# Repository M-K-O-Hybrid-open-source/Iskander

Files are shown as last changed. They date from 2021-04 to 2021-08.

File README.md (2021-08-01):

# Iskander
Iskander is an open source driver for low voltage **DC**, **BLDC**, **PMSM** motors, amde specifically for education and learning.
the repo containts some example ocodes and SIMULINK modeles to help you get started.
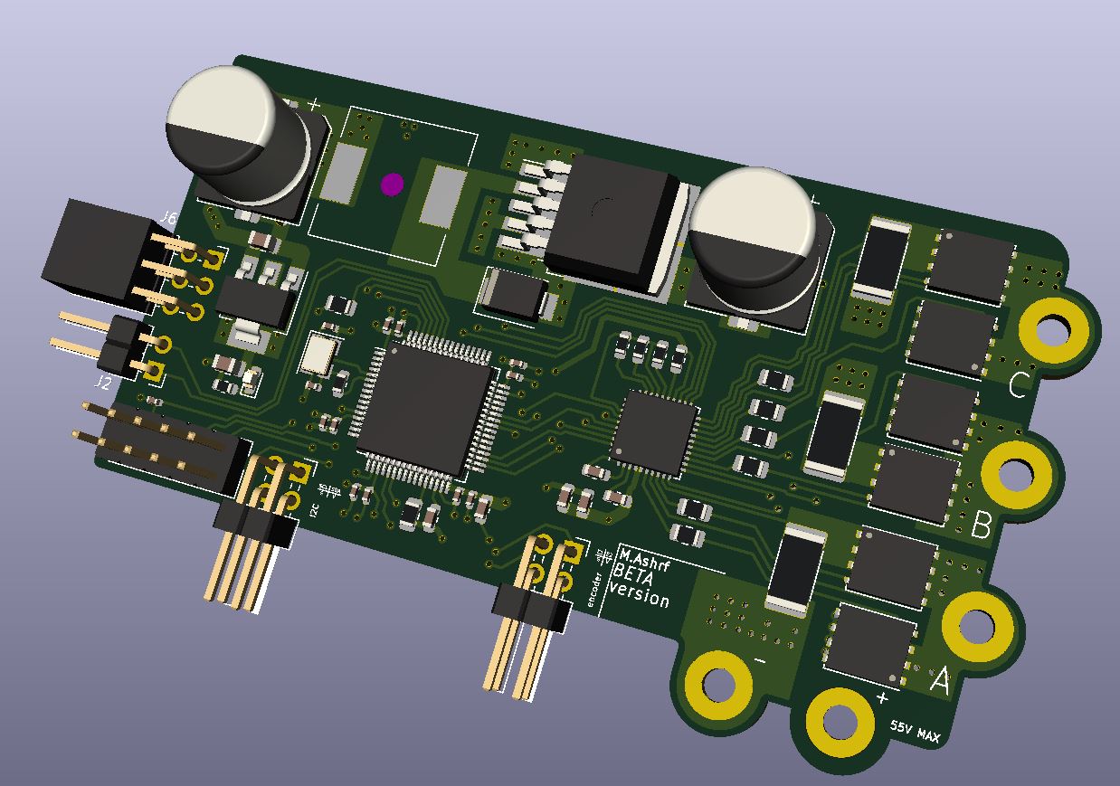
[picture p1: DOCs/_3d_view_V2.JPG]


# Main HARDWARE
- STM32f446RE (main micro-controller)
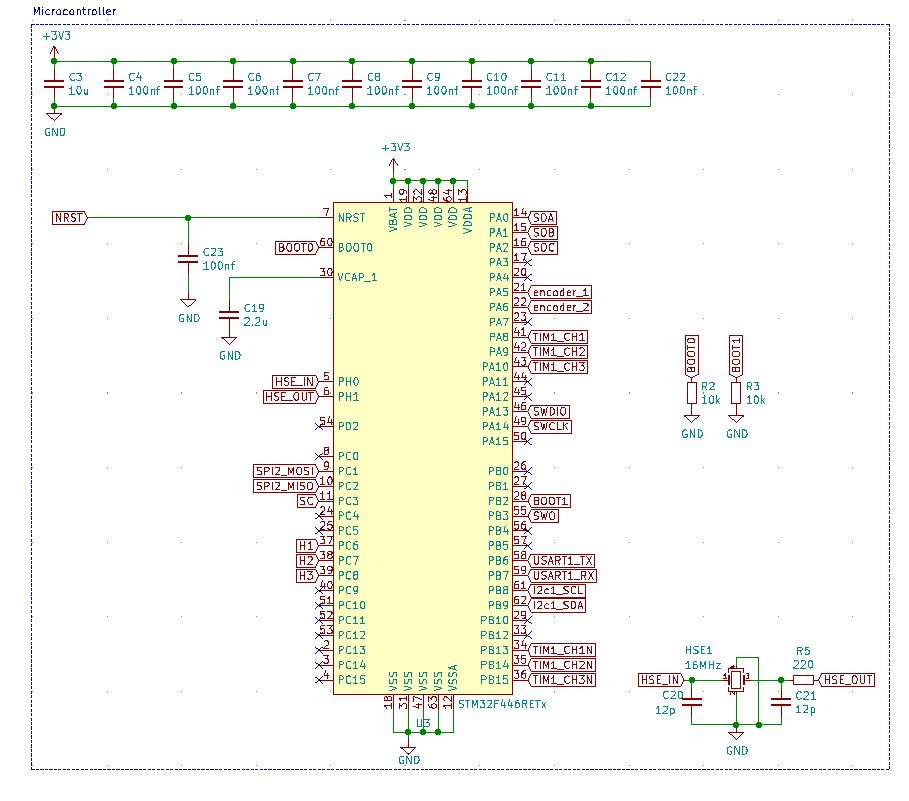
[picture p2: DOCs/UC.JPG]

- DRV8323H (mosfet driver and current sensors)
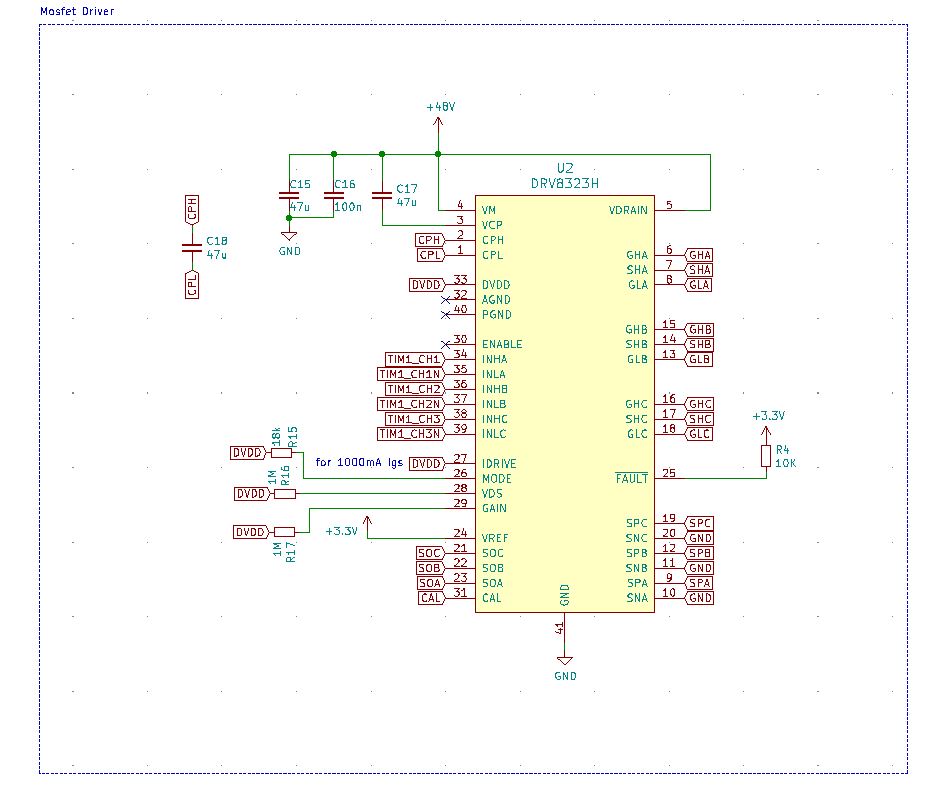
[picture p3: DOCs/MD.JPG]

- CSD19534Q5A (MOSFETs)
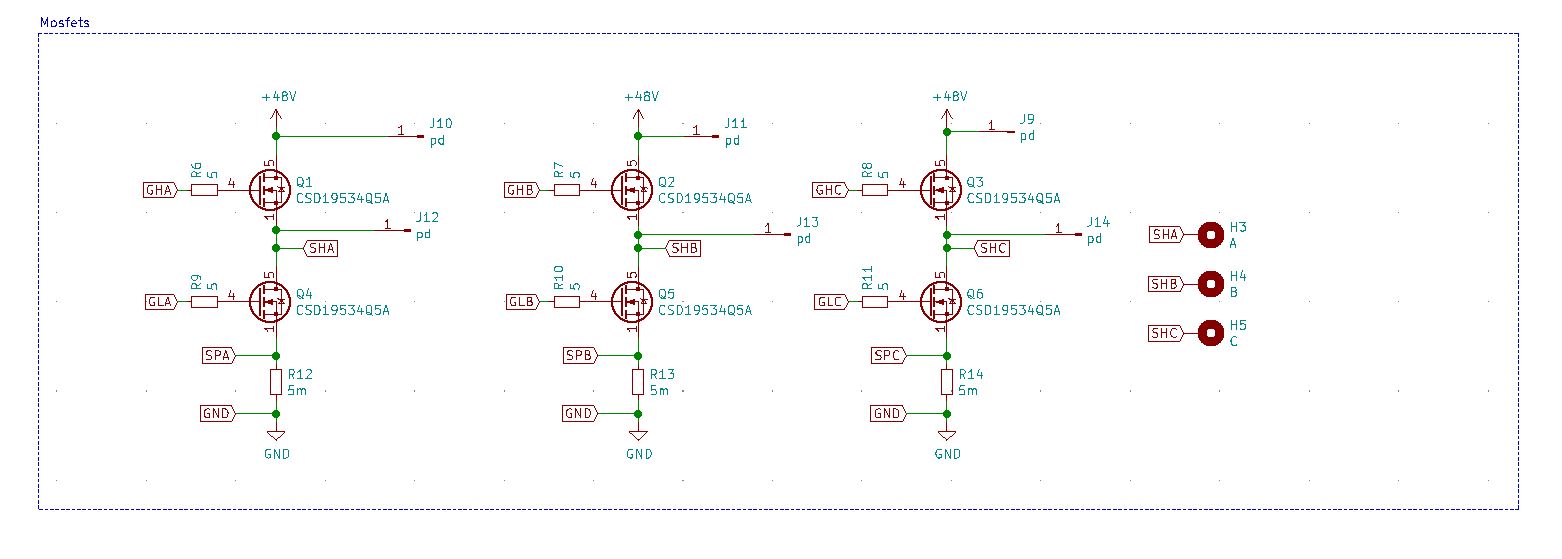
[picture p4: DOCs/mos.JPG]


# the hardware supports the following drives
### DC motor supported drives
- open/closed loop speed control.
- torque control.
- cascadded control.
- position control.

### BLDC motor supported drives
- open/closed loop sensored speed control (Hall effect sensors)
- sensored cascadded control.

### PMSM motor supported drives
- sensored FOC control.
- sensorless control using MRAS as speed estimator(currently under testig).
- sensorless control using EKF as speed estimator(currently under testig).

# PCB layout
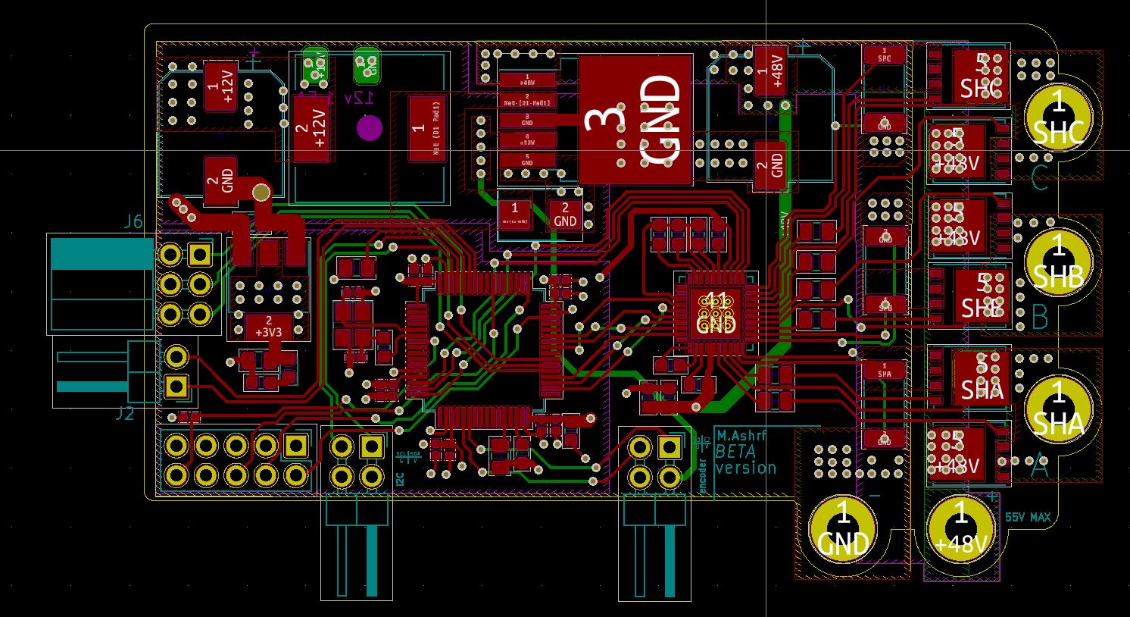
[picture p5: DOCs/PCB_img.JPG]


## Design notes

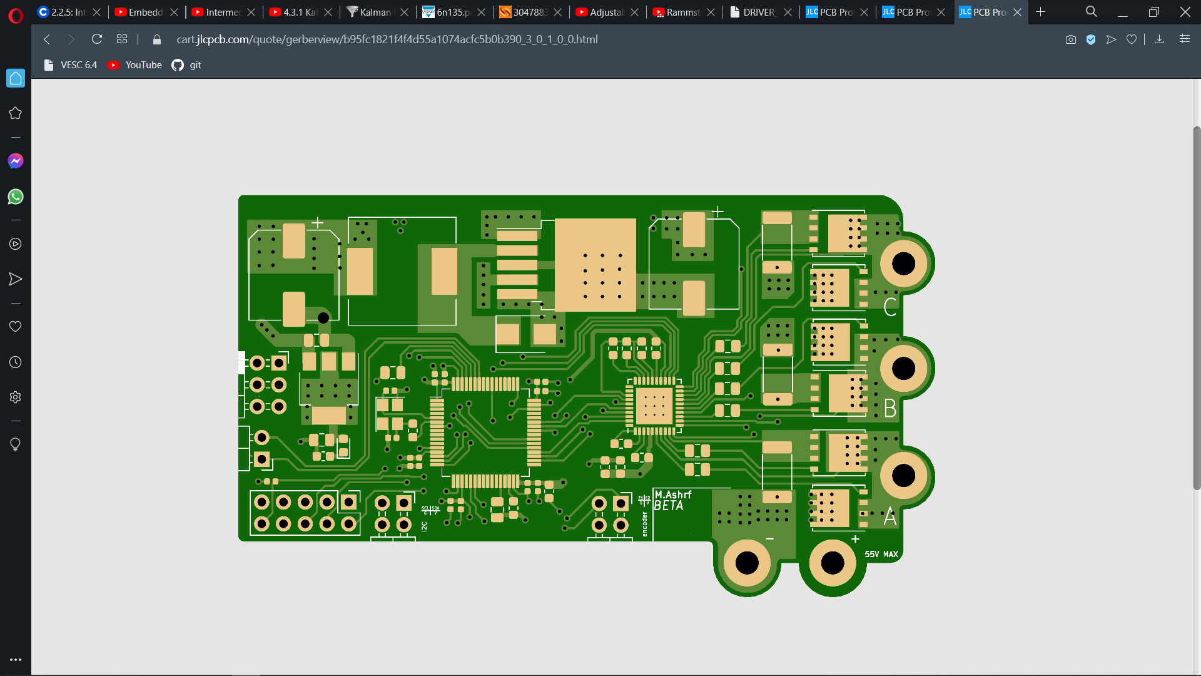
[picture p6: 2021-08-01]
DOCs/Front_img.png

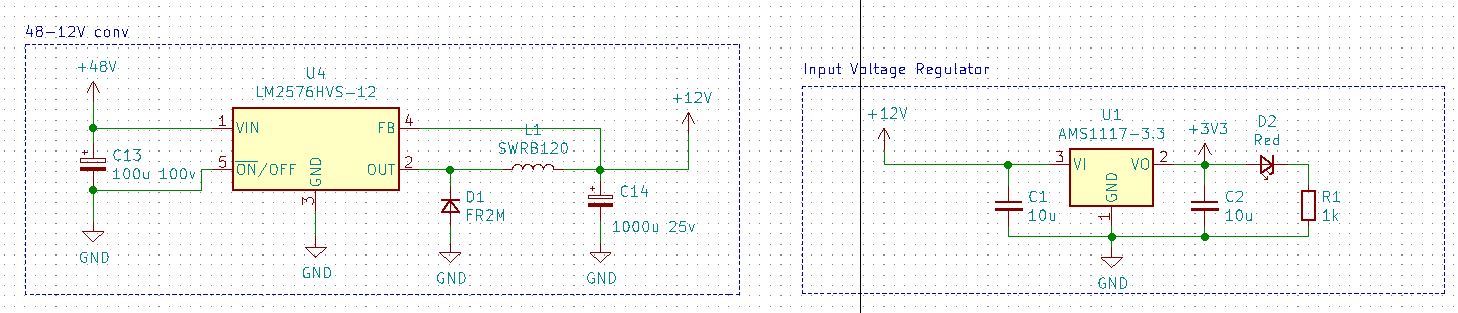
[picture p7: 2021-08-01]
DOCs/Voltage_converters.JPG

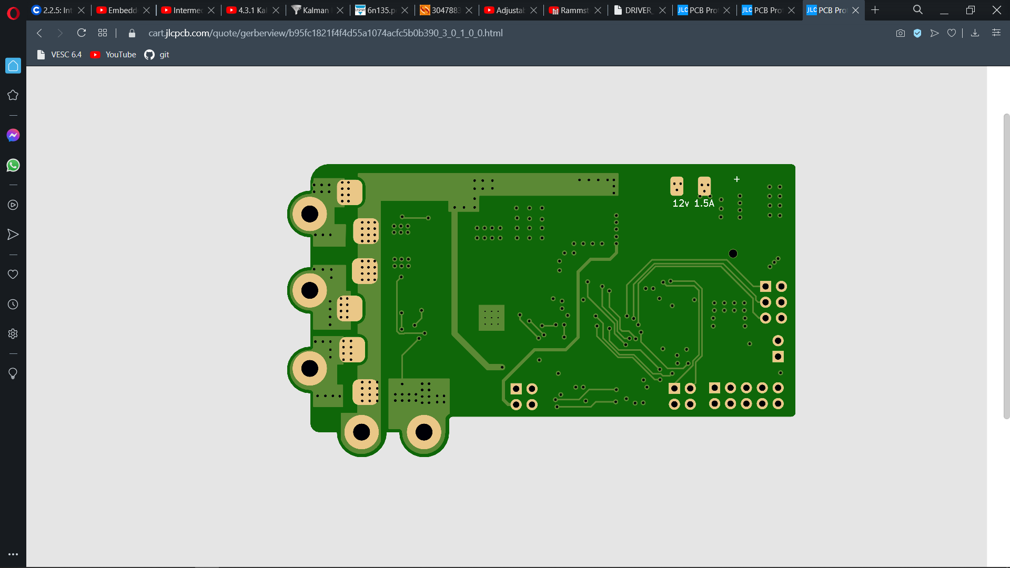
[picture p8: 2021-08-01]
DOCs/Back_img.png

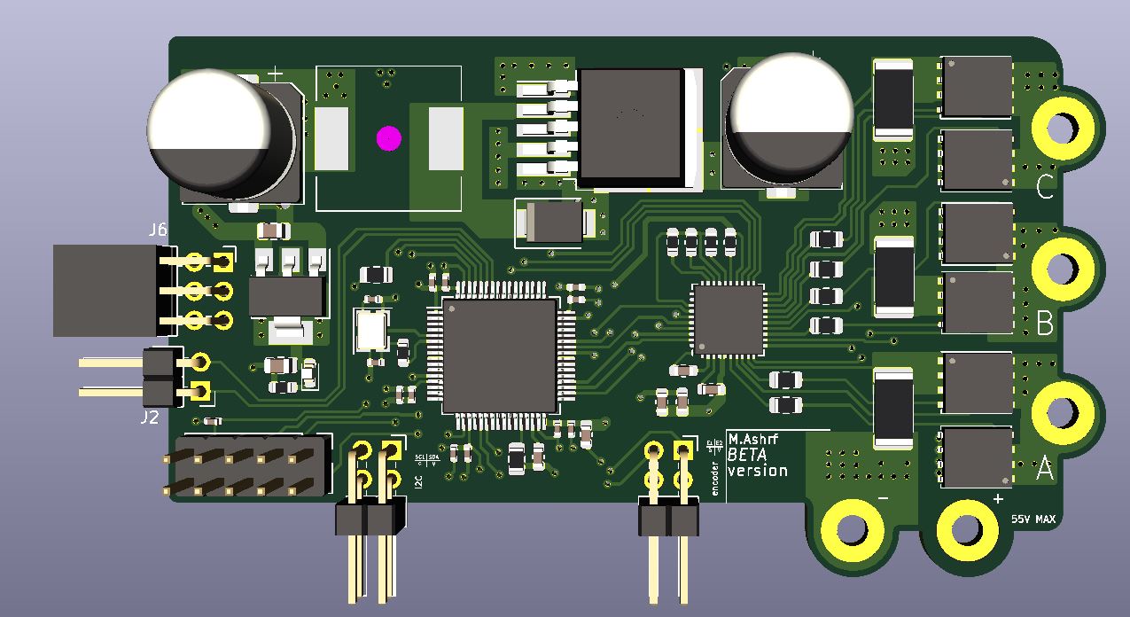
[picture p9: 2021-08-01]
DOCs/_3d_view.JPG

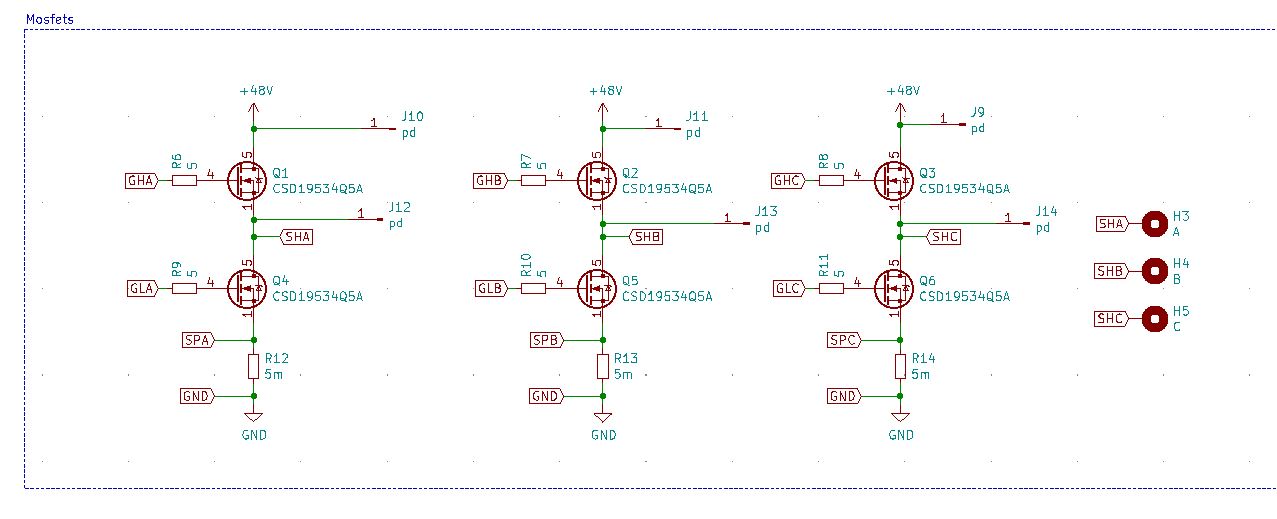
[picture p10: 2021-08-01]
DOCs/Power_stage_sch.JPG

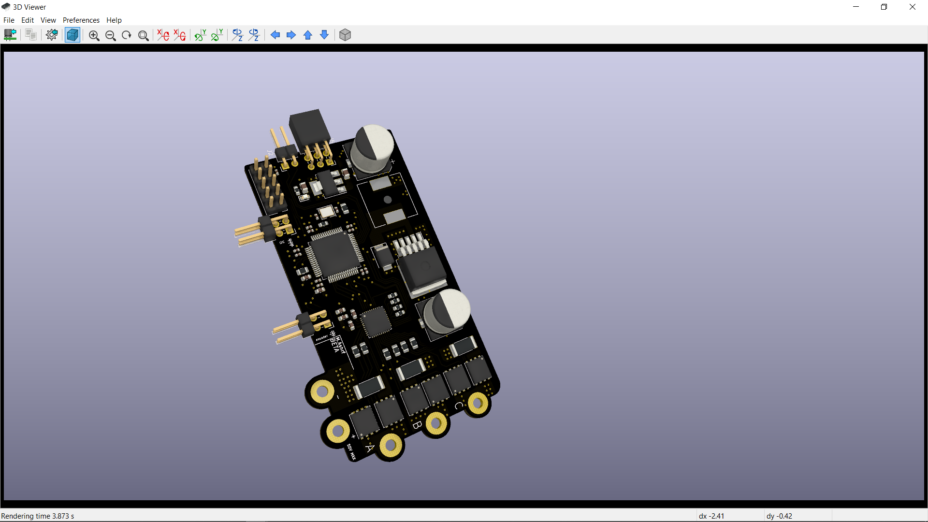
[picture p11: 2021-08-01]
DOCs/_3D_view.png

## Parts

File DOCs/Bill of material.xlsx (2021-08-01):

 | Sourced | References | Value | Footprint | Quantity | Price
1 |  | C13 | 100u 100v | CP_Elec_10x10 | 1 | 0.0760$*5 (at least five units)
2 |  | C14 | 1000u 25v | CP_Elec_10x10 | 1 | 0.0760$*5 (at least five units)
3 |  | C4, C5, C6, C7, C8, C9, C10, C11, C12, C22, C23 | 100nf | C_0402_1005Metric | 11 | $0.0025 *11
4 |  | C20, C21 | 12p | C_0402_1005Metric | 2 | $0.0025 *2
5 |  | C15, C17, C18 | 47u | C_0603_1608Metric | 3 | $0.0025 *3
6 |  | C3 | 10u | C_0603_1608Metric | 1 | $0.0025*1
7 |  | C16 | 100n | C_0603_1608Metric | 1 | $0.0025 *1
8 |  | C19 | 2.2u | C_0603_1608Metric | 1 | $0.0025 *1
9 |  | C1, C2 | 10u | C_0805_2012Metric | 2 | $0.0025 *2
10 |  | R16, R17 | 1M | R_0603_1608Metric | 2 | $0.0025 *2
11 |  | R1 | 1k | R_0603_1608Metric | 1 | $0.0025 *1
12 |  | R4 | 10K | R_0603_1608Metric | 1 | $0.0025 *1
13 |  | R5 | 220 | R_0603_1608Metric | 1 | $0.0025 *1
14 |  | R15 | 18k | R_0603_1608Metric | 1 | $0.0025 *1
15 |  | R6, R7, R8, R9, R10, R11 | 5 | R_0805_2012Metric | 6 | $0.0025 *6
16 |  | R2, R3 | 10k | R_0805_2012Metric | 2 | $0.0025 *2
17 |  | R12, R13, R14 | 5m | R_2512_6332Metric | 3 | $0.0844 *5
18 |  | L1 | SWRB120 | L_12x12mm_H4.5mm | 1 | $0.2525 *1
19 |  | D1 | FR2M | D_SMB | 1 | $0.0796 *1
20 |  | D2 | Red | LED_0603_1608Metric | 1 | $0.0193 *1
21 |  | U3 | STM32F446RETx | LQFP-64_10x10mm_P0.5mm | 1 | $19.932 *1
22 |  | U2 | DRV8323H | QFN-40-1EP_6x6mm_P0.5mm_EP4.6x4.6mm_ThermalVias | 1 | $4.0804 *1
23 |  | U1 | AMS1117-3.3 | SOT-223-3_TabPin2 | 1 | $0.1327 *1
24 |  | U4 | LM2576HVS-12 | TO-263-5_TabPin3 | 1 | $1.6525 *1
25 |  | HSE1 | 16MHz | Crystal_SMD_3225-4Pin_3.2x2.5mm | 1 | $0.0974 *1
26 |  | Q1, Q2, Q3, Q4, Q5, Q6 | CSD19534Q5A | TDSON-8-1 | 6 | $1.4277 *6
27 |  | J2 | USART | PinHeader_1x02_P2.54mm_Horizontal | 1 | .5 EGP
28 |  | J1 | encoder | PinHeader_2x02_P2.54mm_Horizontal | 1 | .5EGP
29 |  | J3 | I2C | PinHeader_2x02_P2.54mm_Horizontal | 1 | .5EGP
30 |  | J5 | Conn_02x05_Odd_Even | PinHeader_2x05_P2.54mm_Vertical | 1 | 1EGP
31 |  | J6 | Hall_EFF | PinSocket_2x03_P2.54mm_Horizontal | 1 | 1EGP
 |  |  |  |  |  | Components SUM = $ 35.039
 |  |  |  |  |  | PCB manufacturing price = 8$

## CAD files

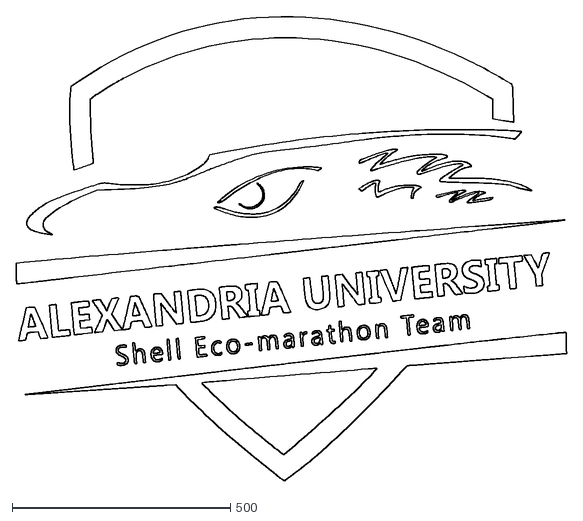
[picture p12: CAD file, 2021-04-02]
logo.dxf
1261.8 x 1064.5

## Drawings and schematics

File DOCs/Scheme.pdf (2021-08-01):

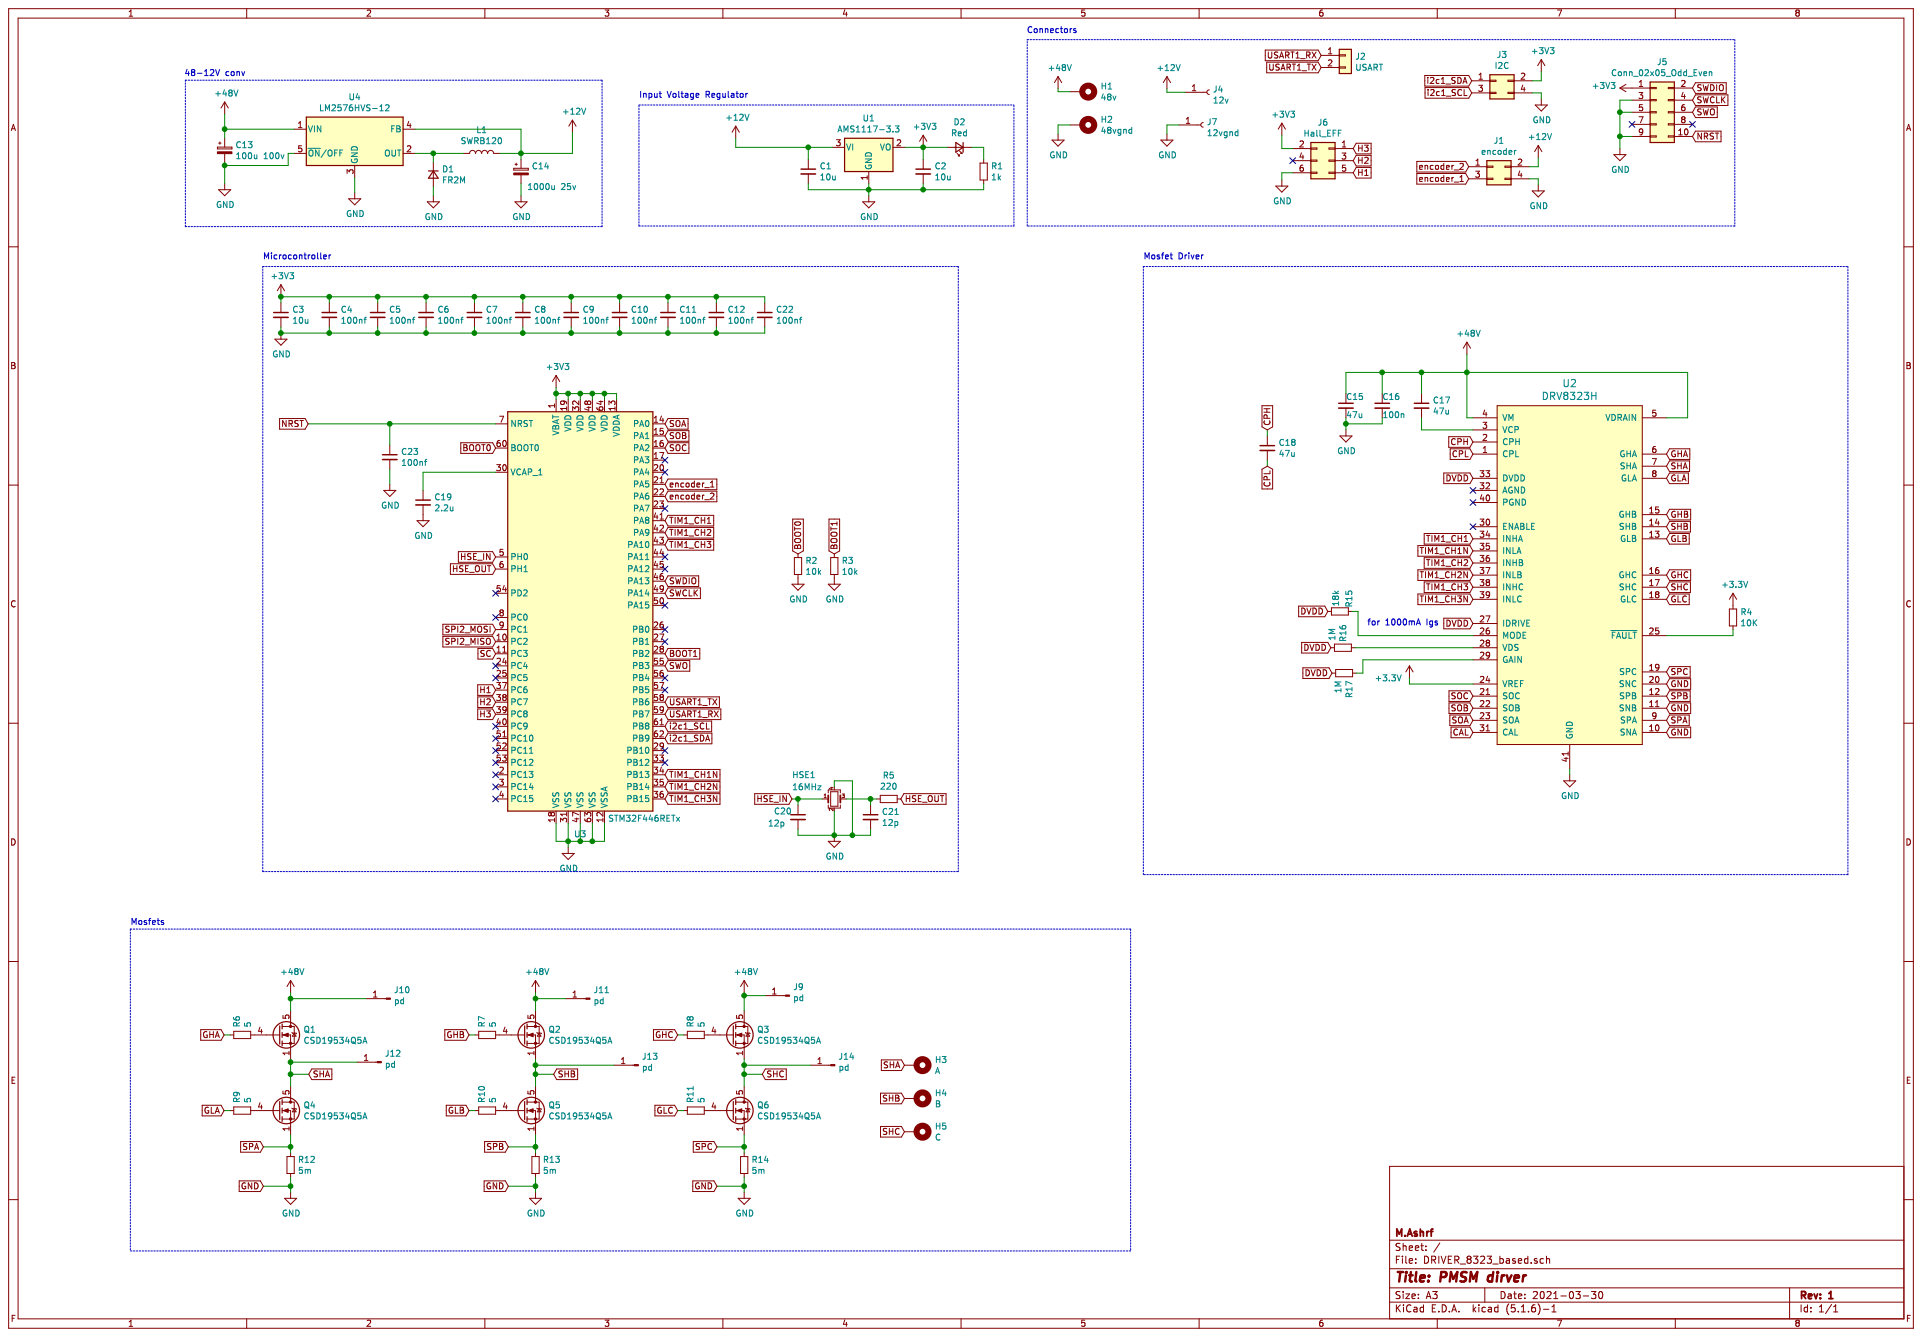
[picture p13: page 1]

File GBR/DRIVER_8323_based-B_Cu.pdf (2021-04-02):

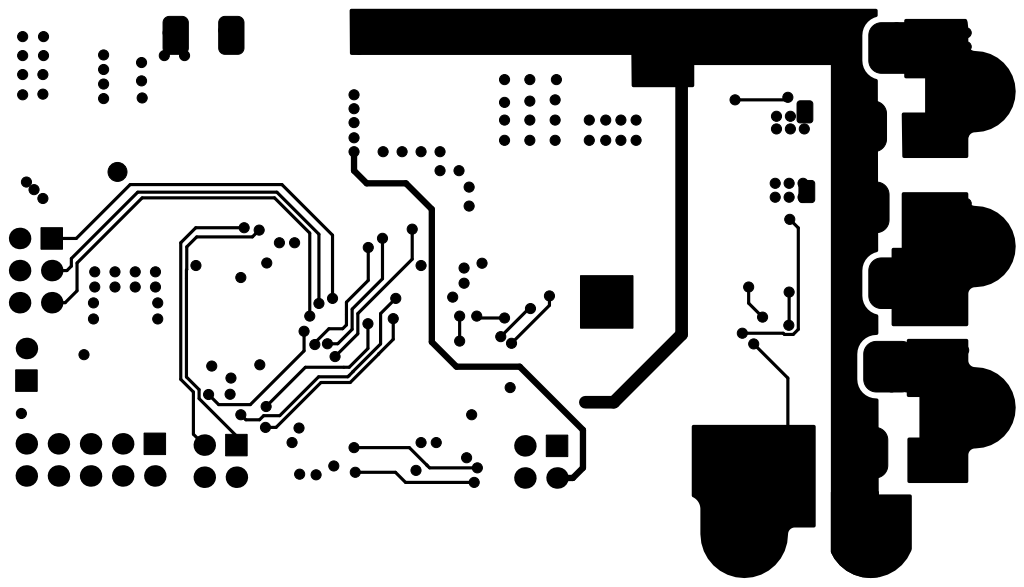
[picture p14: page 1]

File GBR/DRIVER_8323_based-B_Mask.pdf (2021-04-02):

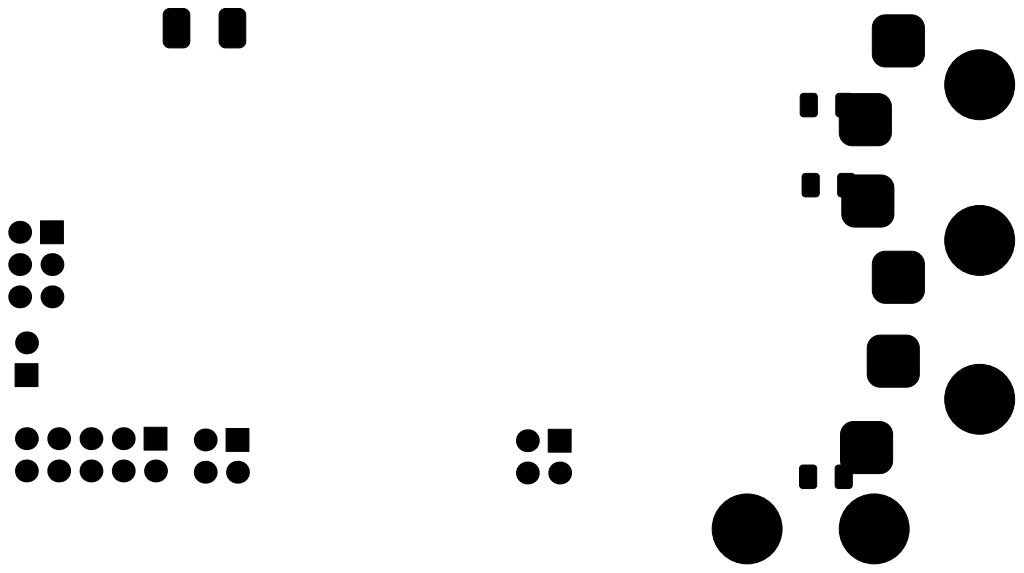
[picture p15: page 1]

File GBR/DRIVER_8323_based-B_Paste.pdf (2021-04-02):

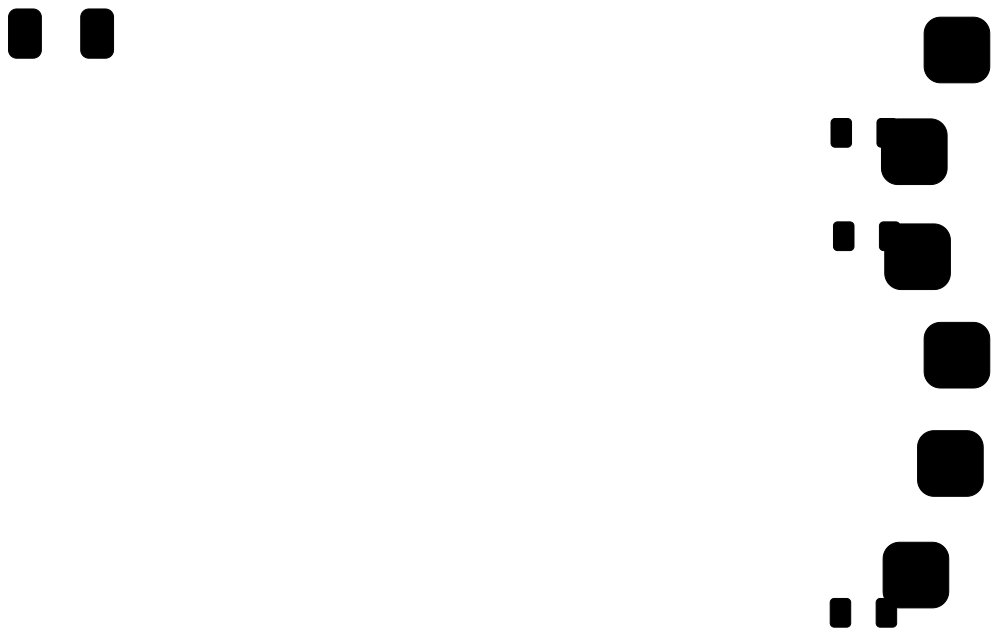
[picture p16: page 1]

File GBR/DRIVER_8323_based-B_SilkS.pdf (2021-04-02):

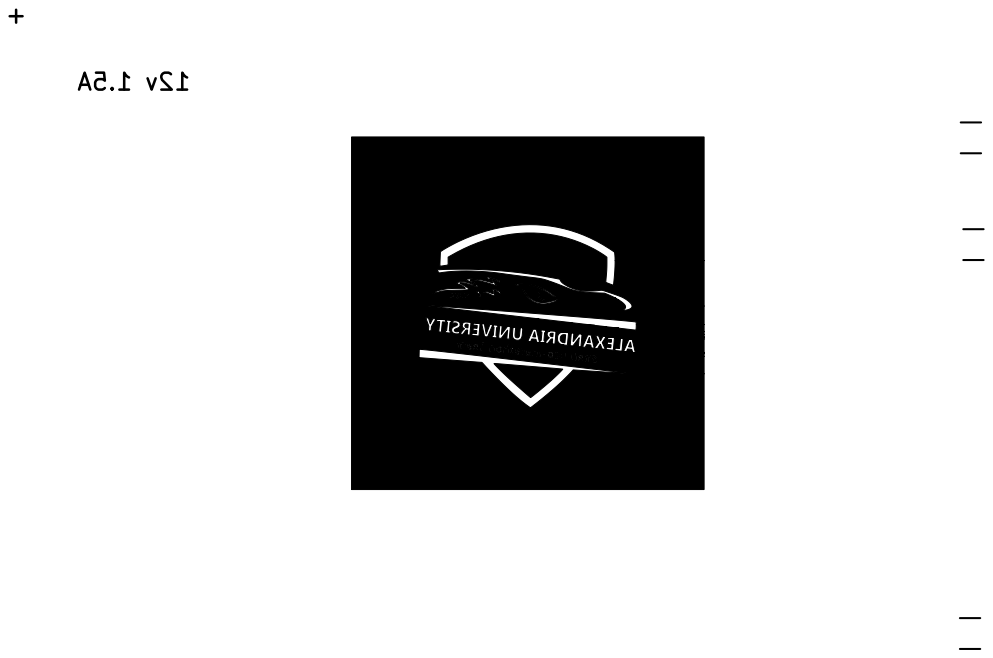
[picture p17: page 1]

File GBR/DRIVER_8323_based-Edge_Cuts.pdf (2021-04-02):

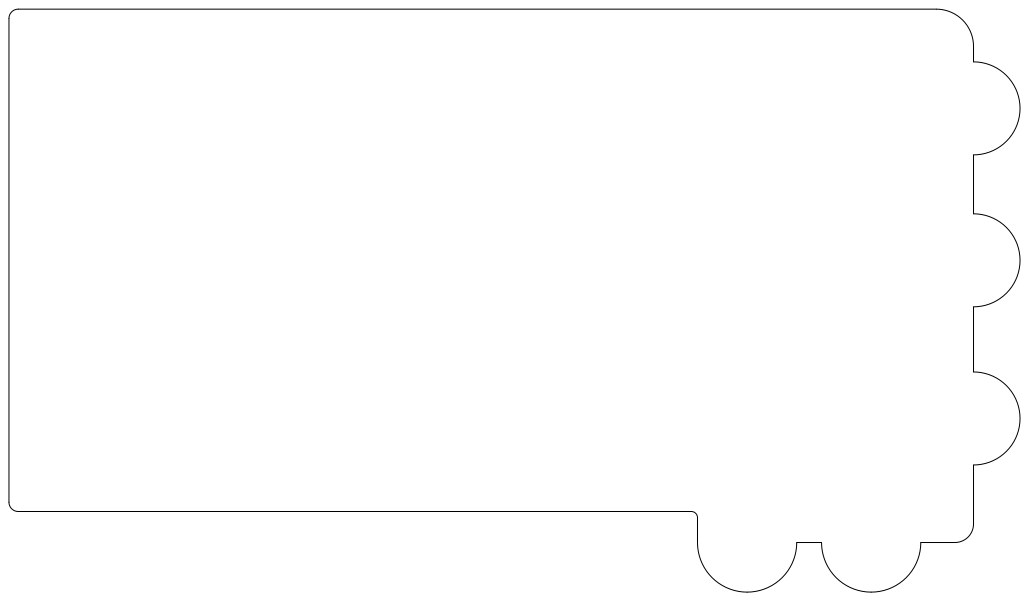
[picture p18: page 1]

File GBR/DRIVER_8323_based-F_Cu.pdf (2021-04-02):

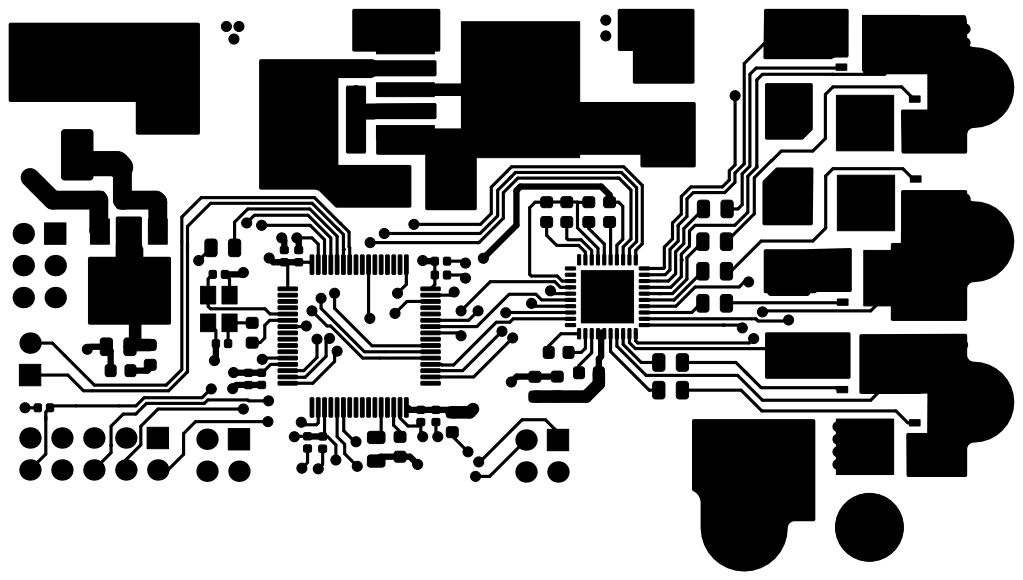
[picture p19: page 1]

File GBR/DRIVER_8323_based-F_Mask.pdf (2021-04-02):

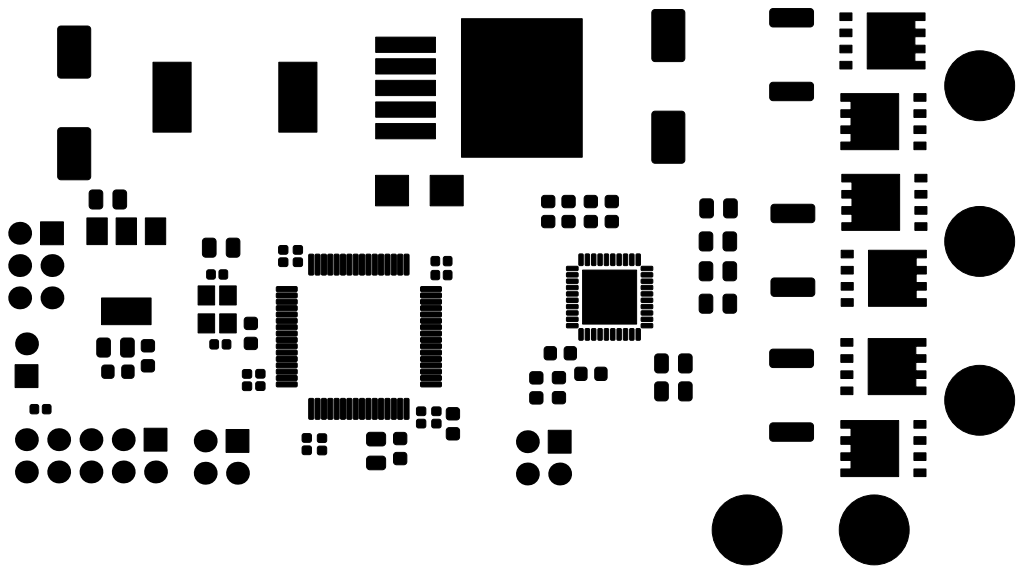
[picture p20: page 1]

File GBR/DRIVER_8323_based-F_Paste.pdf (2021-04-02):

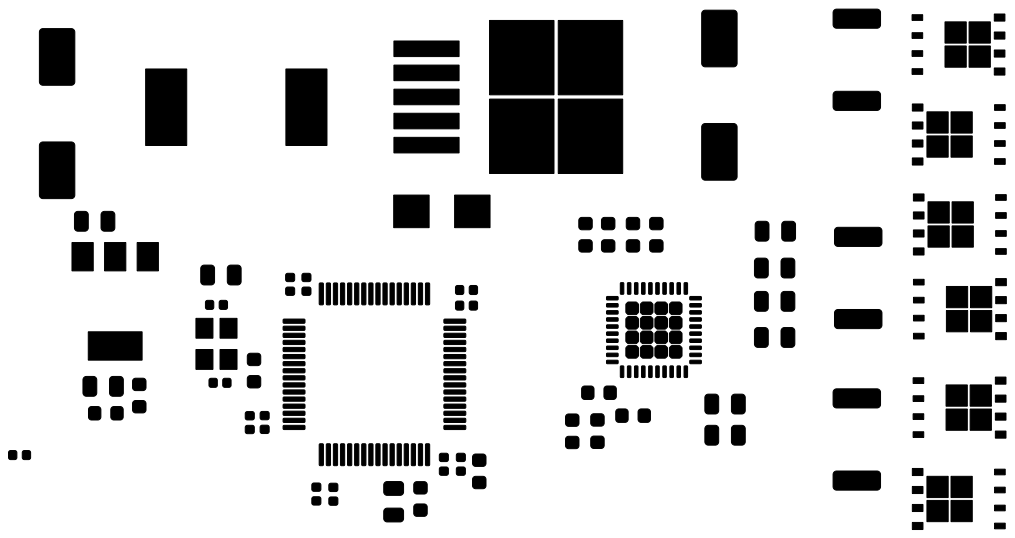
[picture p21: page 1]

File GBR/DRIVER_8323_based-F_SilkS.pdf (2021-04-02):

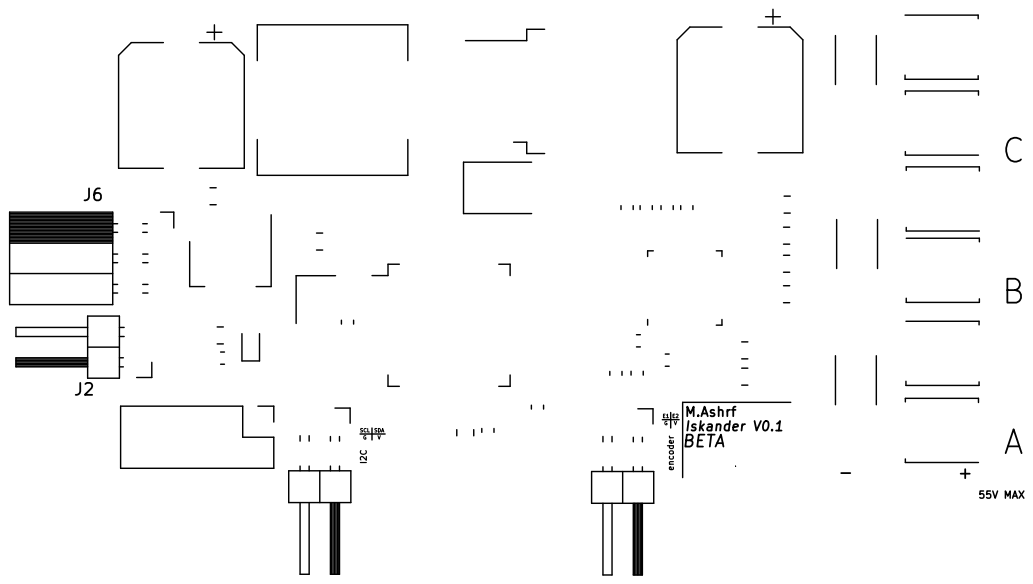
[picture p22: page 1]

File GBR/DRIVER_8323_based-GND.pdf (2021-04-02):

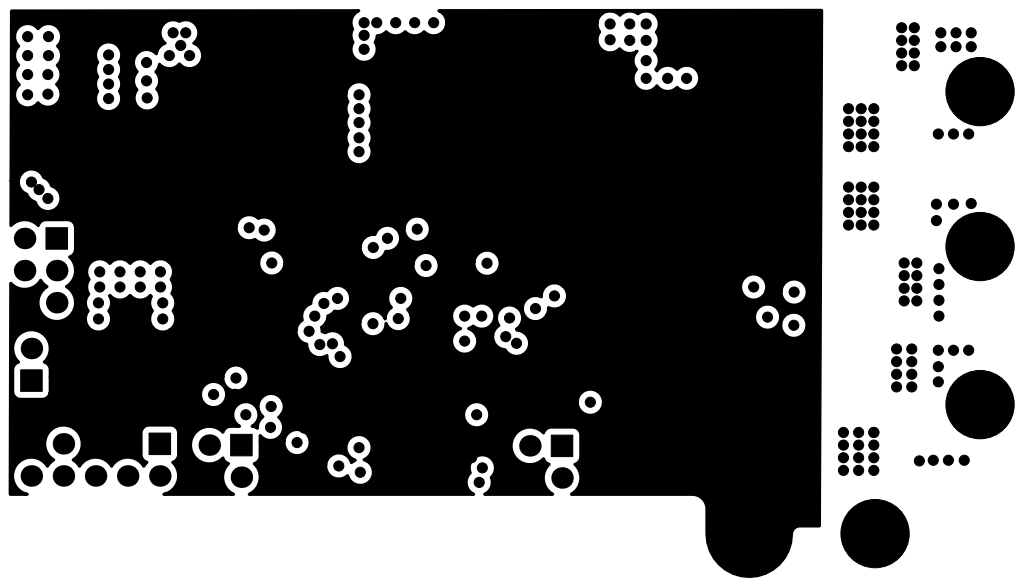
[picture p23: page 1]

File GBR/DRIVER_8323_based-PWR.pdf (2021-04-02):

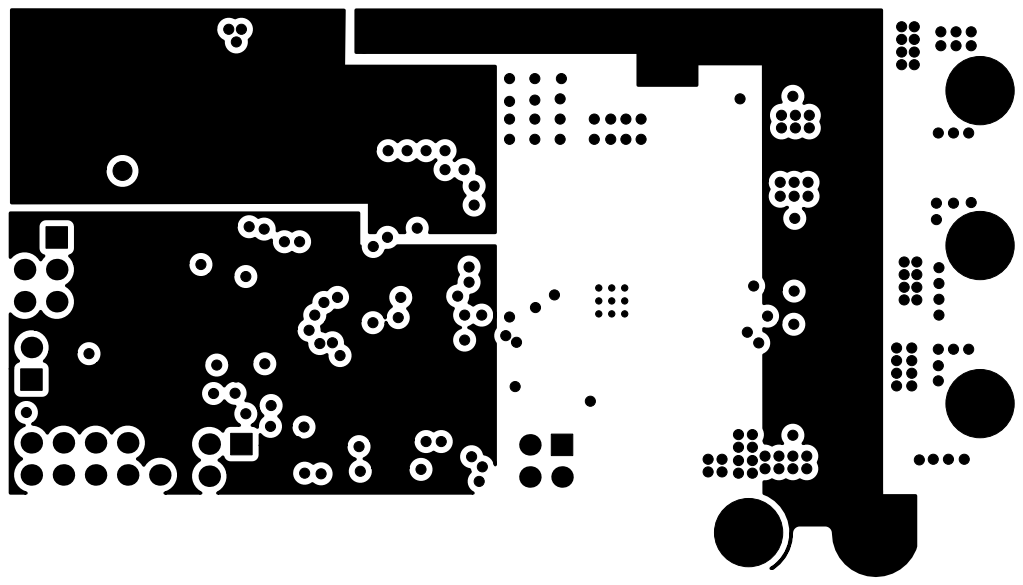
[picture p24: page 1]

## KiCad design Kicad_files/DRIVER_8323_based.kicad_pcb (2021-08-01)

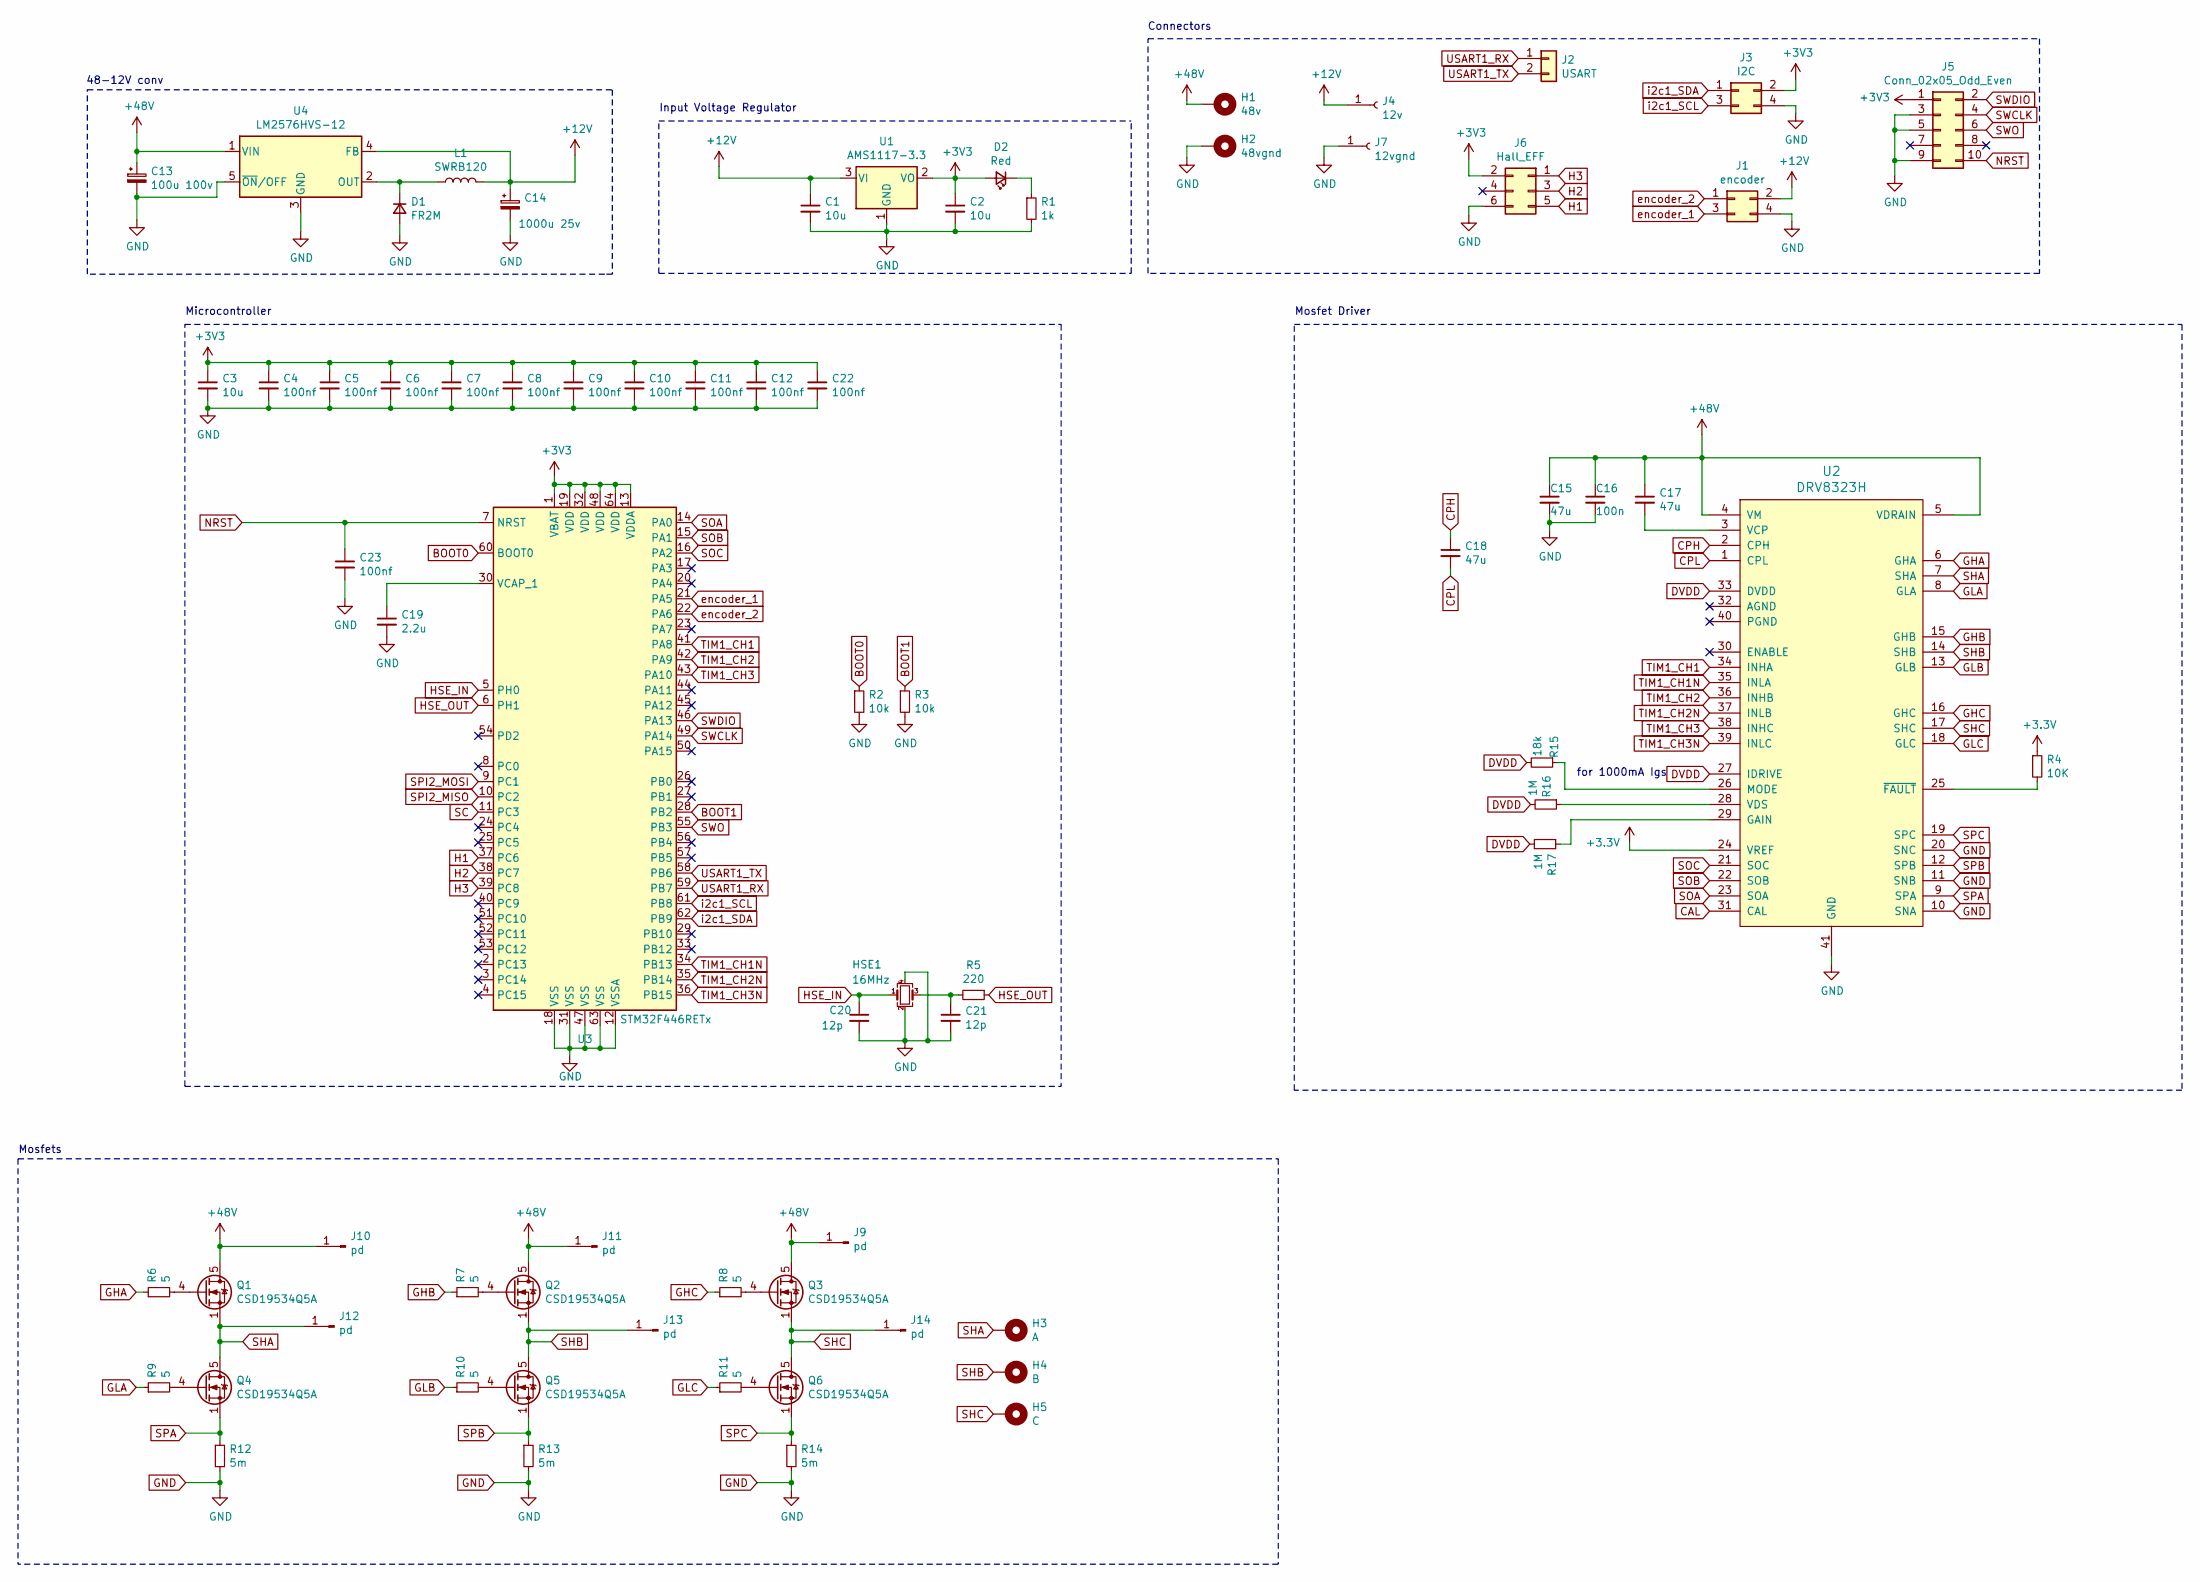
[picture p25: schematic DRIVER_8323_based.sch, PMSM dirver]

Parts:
C1, C2: 10u; C_0805_2012Metric
C3: 10u; C_0603_1608Metric
C4, C5, C6, C7, C8, C9, C10, C11, C12, C22, C23: 100nf; C_0402_1005Metric
C13: 100u 100v; CP_Elec_10x10
C14: 1000u 25v; CP_Elec_10x10
C15, C17, C18: 47u; C_0603_1608Metric
C16: 100n; C_0603_1608Metric
C19: 2.2u; C_0603_1608Metric
C20, C21: 12p; C_0402_1005Metric
D1: FR2M; D_SMB
D2: Red; LED_0603_1608Metric
H1: 48v; MountingHole_2.7mm_Pad
H2: 48vgnd; MountingHole_2.7mm_Pad
H3: A; MountingHole_2.7mm_Pad
H4: B; MountingHole_2.7mm_Pad
H5: C; MountingHole_2.7mm_Pad
HSE1: 16MHz; Crystal_SMD_3225-4Pin_3.2x2.5mm
J1: encoder; PinHeader_2x02_P2.54mm_Horizontal
J2: USART; PinHeader_1x02_P2.54mm_Horizontal
J3: I2C; PinHeader_2x02_P2.54mm_Horizontal
J4: 12v; SolderWirePad_1x01_SMD_1x2mm
J5: Conn_02x05_Odd_Even; PinHeader_2x05_P2.54mm_Vertical
J6: Hall_EFF; PinSocket_2x03_P2.54mm_Horizontal
J7: 12vgnd; SolderWirePad_1x01_SMD_1x2mm
J9, J10, J11, J12, J13, J14: pd; SolderWirePad_1x01_SMD_1x2mm
L1: SWRB120; L_12x12mm_H4.5mm
Q1, Q2, Q3, Q4, Q5, Q6: CSD19534Q5A; TDSON-8-1
R1: 1k; R_0603_1608Metric
R2, R3: 10k; R_0805_2012Metric
R4: 10K; R_0603_1608Metric
R5: 220; R_0603_1608Metric
R6, R7, R8, R9, R10, R11: 5; R_0805_2012Metric
R12, R13, R14: 5m; R_2512_6332Metric
R15: 18k; R_0603_1608Metric
R16, R17: 1M; R_0603_1608Metric
U1: AMS1117-3.3; SOT-223-3_TabPin2
U2: DRV8323H; QFN-40-1EP_6x6mm_P0.5mm_EP4.6x4.6mm_ThermalVias
U3: STM32F446RETx; LQFP-64_10x10mm_P0.5mm
U4: LM2576HVS-12; TO-263-5_TabPin3

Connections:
+12V: C1.1, C14.1, J1.2, J4.1, L1.2, U1.3 (VI), U4.4 (FB)
+48V: C13.1, C15.1, C16.1, C17.1, H1.1, J9.1, J10.1, J11.1, Q1.5 (D), Q2.5 (D), Q3.5 (D), U2.4 (VM), U2.5 (VDRAIN), U4.1 (VIN)
BOOT0: R2.1, U3.60 (BOOT0)
BOOT1: R3.1, U3.28 (PB2)
CAL: U2.31 (CAL)
CPH: C18.1, U2.2 (CPH)
CPL: C18.2, U2.1 (CPL)
DVDD: R15.2, R16.2, R17.2, U2.27 (IDRIVE), U2.33 (DVDD)
GHA: R6.1, U2.6 (GHA)
GHB: R7.1, U2.15 (GHB)
GHC: R8.1, U2.16 (GHC)
GLA: R9.1, U2.8 (GLA)
GLB: R10.1, U2.13 (GLB)
GLC: R11.1, U2.18 (GLC)
GND: C1.2, C2.2, C3.2, C4.2, C5.2, C6.2, C7.2, C8.2, C9.2, C10.2, C11.2, C12.2, C13.2, C14.2, C15.2, C16.2, C19.2, C20.2, C21.2, C22.2, C23.2, D1.2 (A), H2.1, HSE1.2, HSE1.4, J1.4, J3.4, J5.3, J5.5, J5.9, J6.6, J7.1, R1.2, R2.2, R3.2, R12.2, R13.2, R14.2, U1.1 (GND), U2.10 (SNA), U2.11 (SNB), U2.20 (SNC), U2.41 (GND), U3.12 (VSSA), U3.18 (VSS), U3.31 (VSS), U3.47 (VSS), U3.63 (VSS), U4.3 (GND), U4.5 (~ON~/OFF)
H1: J6.5, U3.37 (PC6)
H2: J6.3, U3.38 (PC7)
H3: J6.1, U3.39 (PC8)
HSE_IN: C20.1, HSE1.1, U3.5 (PH0)
HSE_OUT: R5.1, U3.6 (PH1)
NRST: C23.1, J5.10, U3.7 (NRST)
unnamed: C17.2, U2.3 (VCP)
unnamed: C19.1, U3.30 (VCAP_1)
unnamed: C21.1, HSE1.3, R5.2
unnamed: D1.1 (K), L1.1, U4.2 (OUT)
unnamed: D2.1 (K), R1.1
unnamed: Q1.4 (G), R6.2
unnamed: Q2.4 (G), R7.2
unnamed: Q3.4 (G), R8.2
unnamed: Q4.4 (G), R9.2
unnamed: Q5.4 (G), R10.2
unnamed: Q6.4 (G), R11.2
unnamed: R4.2, U2.25 (~FAULT)
unnamed: R15.1, U2.26 (MODE)
unnamed: R16.1, U2.28 (VDS)
unnamed: R17.1, U2.29 (GAIN)
SC: U3.11 (PC3)
SHA: H3.1, J12.1, Q1.1 (S), Q1.2 (S), Q1.3 (S), Q4.5 (D), U2.7 (SHA)
SHB: H4.1, J13.1, Q2.1 (S), Q2.2 (S), Q2.3 (S), Q5.5 (D), U2.14 (SHB)
SHC: H5.1, J14.1, Q3.1 (S), Q3.2 (S), Q3.3 (S), Q6.5 (D), U2.17 (SHC)
SOA: U2.23 (SOA), U3.14 (PA0)
SOB: U2.22 (SOB), U3.15 (PA1)
SOC: U2.21 (SOC), U3.16 (PA2)
SPA: Q4.1 (S), Q4.2 (S), Q4.3 (S), R12.1, U2.9 (SPA)
SPB: Q5.1 (S), Q5.2 (S), Q5.3 (S), R13.1, U2.12 (SPB)
SPC: Q6.1 (S), Q6.2 (S), Q6.3 (S), R14.1, U2.19 (SPC)
SPI2_MISO: U3.10 (PC2)
SPI2_MOSI: U3.9 (PC1)
SWCLK: J5.4, U3.49 (PA14)
SWDIO: J5.2, U3.46 (PA13)
SWO: J5.6, U3.55 (PB3)
TIM1_CH1: U2.34 (INHA), U3.41 (PA8)
TIM1_CH1N: U2.35 (INLA), U3.34 (PB13)
TIM1_CH2: U2.36 (INHB), U3.42 (PA9)
TIM1_CH2N: U2.37 (INLB), U3.35 (PB14)
TIM1_CH3: U2.38 (INHC), U3.43 (PA10)
TIM1_CH3N: U2.39 (INLC), U3.36 (PB15)
USART1_RX: J2.1, U3.59 (PB7)
USART1_TX: J2.2, U3.58 (PB6)
encoder_1: J1.3, U3.21 (PA5)
encoder_2: J1.1, U3.22 (PA6)
i2c1_SCL: J3.3, U3.61 (PB8)
i2c1_SDA: J3.1, U3.62 (PB9)

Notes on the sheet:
Input Voltage Regulator
Microcontroller
Connectors
Mosfet Driver
for 1000mA Igs
Mosfets
48-12V conv

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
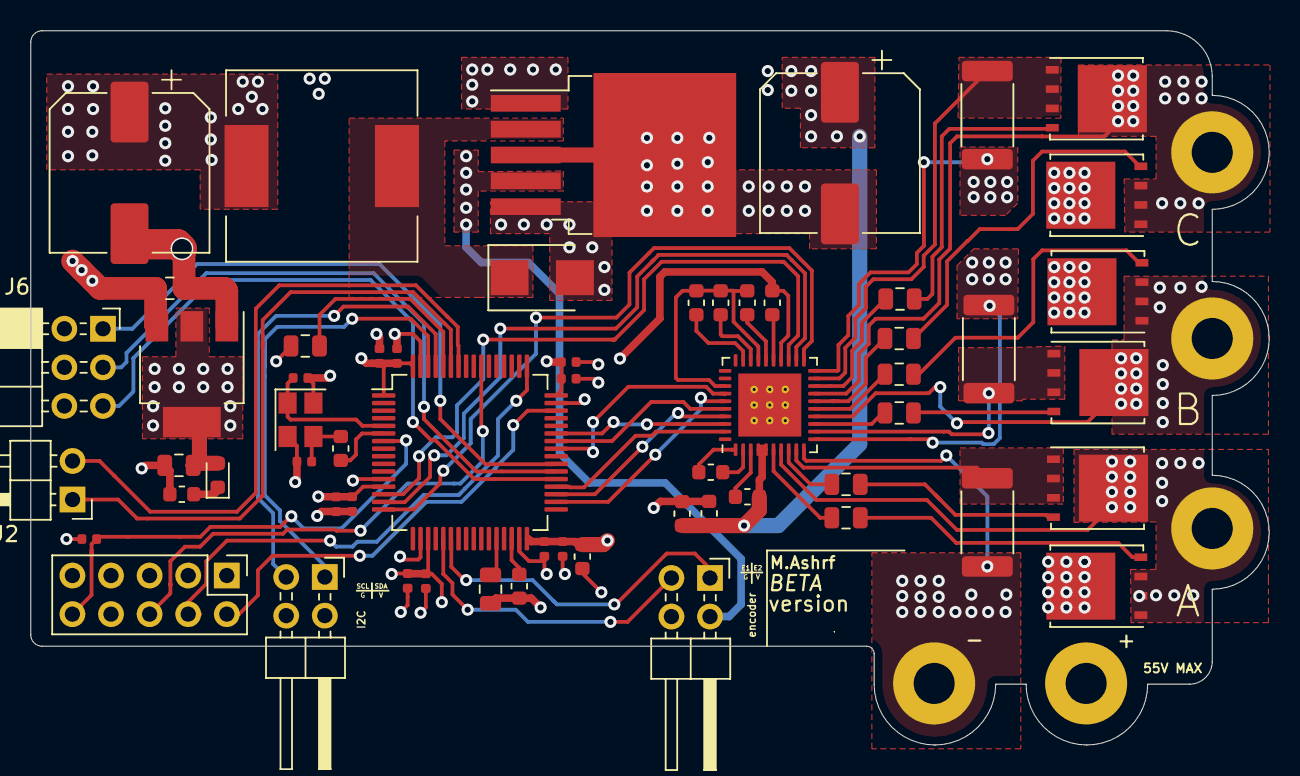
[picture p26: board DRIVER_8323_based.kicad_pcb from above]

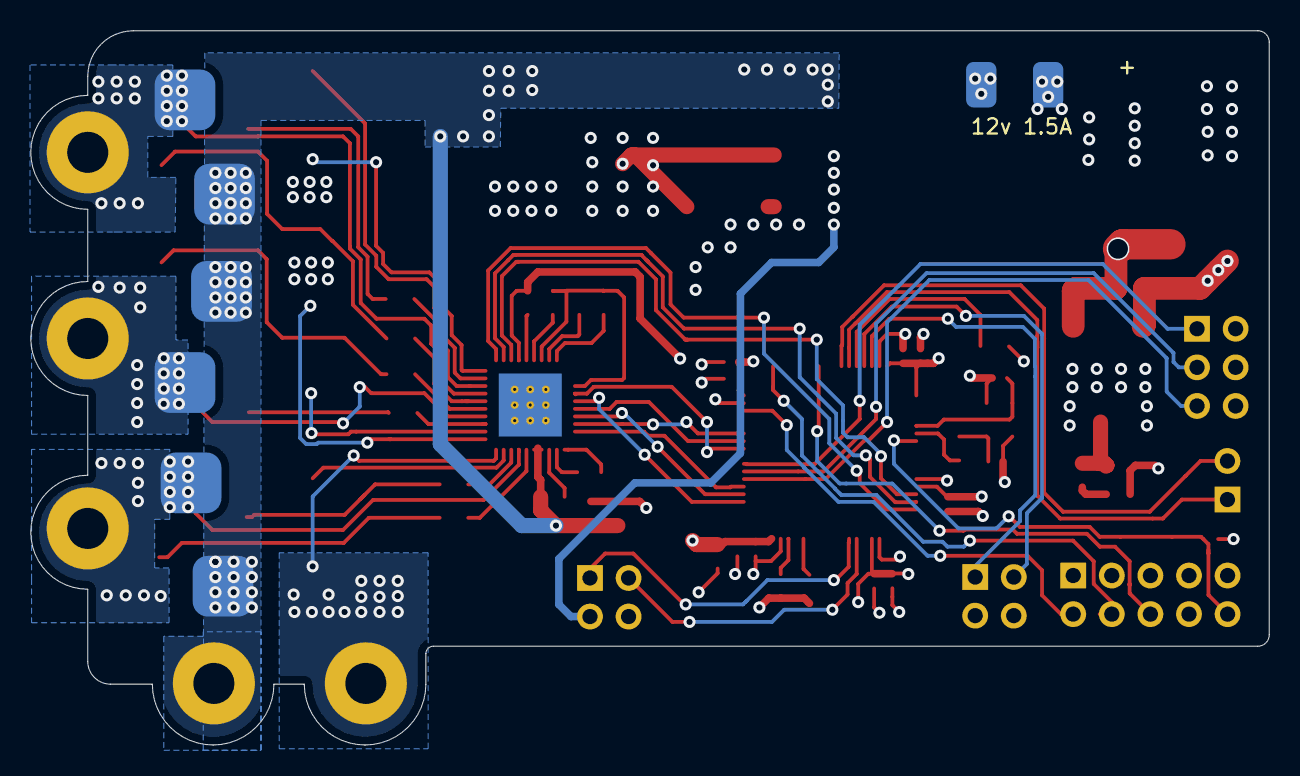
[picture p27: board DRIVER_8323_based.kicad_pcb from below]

Board: 4 copper layers, 81.5 x 47.0 mm, 72 parts (8 on the bottom side), 60 nets.

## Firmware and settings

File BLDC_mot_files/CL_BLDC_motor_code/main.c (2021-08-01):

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

/* Includes ------------------------------------------------------------------*/
#include "main.h"

/* USER CODE BEGIN Includes */
#include <stdint.h>
#include "string.h"
#include "stdlib.h"
#include "stdarg.h"

/* USER CODE END Includes */

/* USER CODE BEGIN PTD */
#include "PID.h"

/* USER CODE END PTD */

/* USER CODE BEGIN PD */
#define PI 3.14159265

/* Controller parameters */
#define PID_KP_I  100.0f
#define PID_KI_I  20.0f
#define PID_KD_I  0.0f

#define PID_TAU_I 0.02f

#define PID_LIM_MIN_I  0.0f
#define PID_LIM_MAX_I  1800.0f

#define PID_LIM_MIN_INT_I  0.0f
#define PID_LIM_MAX_INT_I  1700.0f

#define SAMPLE_TIME_S 0.0001f					// f = clk_freq/(Period*INC) = 72e6/(720*10) = 1e4 Hz = .0001 sec




/* USER CODE END PD */

/* USER CODE BEGIN PM */
float map(float x, float in_min, float in_max, float out_min, float out_max)
{
	return (x - in_min) * (out_max - out_min) / (in_max - in_min) + out_min;
}
/* USER CODE END PM */

ADC_HandleTypeDef hadc1;
DMA_HandleTypeDef hdma_adc1;

TIM_HandleTypeDef htim1;
TIM_HandleTypeDef htim2;
TIM_HandleTypeDef htim3;

UART_HandleTypeDef huart1;

/* USER CODE BEGIN PV */
uint16_t ADC_VALs[4];
uint8_t sensor[3];
uint8_t STEP=0;


uint32_t time_tehif=0;
double time_diff=0;
double speed=0;
uint8_t Pole_P = 1;

float mes_I=0;
	

/* USER CODE END PV */

void SystemClock_Config(void);
static void MX_GPIO_Init(void);
static void MX_DMA_Init(void);
static void MX_ADC1_Init(void);
static void MX_TIM1_Init(void);
static void MX_TIM2_Init(void);
static void MX_TIM3_Init(void);
static void MX_USART1_UART_Init(void);
/* USER CODE BEGIN PFP */
void FIND_MOTOR_STEP(void);
void APPLY_THE_PWMs(uint8_t step);
/* USER CODE END PFP */

/* USER CODE BEGIN 0 */
void printMsg(char *msg, ...){
 char buff[80];
 //#ifdef DEBUG_UART
 
 va_list args;
 va_start(args,msg);
 vsprintf(buff,msg,args);
 
 for(int i=0;i<strlen(buff);i++)
 {
	 USART1->DR = buff[i];
	 while(!(USART1->SR & USART_SR_TXE));
	}
} 

/* Initialisec PID controller */

PIDController pid_I = { PID_KP_I, PID_KI_I, -PID_KD_I,
												PID_TAU_I,
												PID_LIM_MIN_I, PID_LIM_MAX_I,
												PID_LIM_MIN_INT_I, PID_LIM_MAX_INT_I,
												SAMPLE_TIME_S };


/* USER CODE END 0 */

/**
  * @brief  The application entry point.
  * @retval int
  */
int main(void)
{
  /* MCU Configuration--------------------------------------------------------*/

  /* Reset of all peripherals, Initializes the Flash interface and the Systick. */
  HAL_Init();

  /* Configure the system clock */
  SystemClock_Config();

  /* Initialize all configured peripherals */
  MX_GPIO_Init();
  MX_DMA_Init();
  MX_ADC1_Init();
  MX_TIM1_Init();
  MX_TIM2_Init();
  MX_TIM3_Init();
  MX_USART1_UART_Init();
  /* USER CODE BEGIN 2 */
	
	HAL_ADC_Start_DMA(&hadc1,( uint32_t *)ADC_VALs,4);

	// TIMER init	
	HAL_TIM_PWM_Start(&htim1, TIM_CHANNEL_1);
	HAL_TIM_PWM_Start(&htim2, TIM_CHANNEL_1);	// turn on complementary channel
	
	HAL_TIM_PWM_Start(&htim1, TIM_CHANNEL_2);
	HAL_TIM_PWM_Start(&htim2, TIM_CHANNEL_2); // turn on complementary channel
	
	HAL_TIM_PWM_Start(&htim1, TIM_CHANNEL_3);
	HAL_TIM_PWM_Start(&htim2, TIM_CHANNEL_3); // turn on complementary channel

	
	__HAL_TIM_SET_COMPARE(&htim1, TIM_CHANNEL_1,(uint32_t)0);
	__HAL_TIM_SET_COMPARE(&htim2, TIM_CHANNEL_1,(uint32_t)0);

	__HAL_TIM_SET_COMPARE(&htim1, TIM_CHANNEL_2,(uint32_t)0);
	__HAL_TIM_SET_COMPARE(&htim2, TIM_CHANNEL_2,(uint32_t)0);

	__HAL_TIM_SET_COMPARE(&htim1, TIM_CHANNEL_3,(uint32_t)0);
	__HAL_TIM_SET_COMPARE(&htim2, TIM_CHANNEL_3,(uint32_t)0);
	
	HAL_TIM_Base_Start_IT(&htim3);
	PIDController_Init(&pid_I);

  /* USER CODE END 2 */

  /* Infinite loop */
  /* USER CODE BEGIN WHILE */
  while (1)
  {
    /* USER CODE END WHILE */
		mes_I =  map(ADC_VALs[0],0,4048,0,20);;
    /* USER CODE BEGIN 3 */
  }
  /* USER CODE END 3 */
}

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
/* USER CODE BEGIN 4 */


// The time update for the controller-one second only for NOW, every 100 micro-second
void HAL_TIM_PeriodElapsedCallback(TIM_HandleTypeDef *htim) {
	UNUSED(htim);
	if (htim->Instance == TIM3) {
		HAL_GPIO_TogglePin(GPIOC,GPIO_PIN_13);
		time_tehif++;
		PIDController_Update(&pid_I, 10, mes_I);
		__HAL_TIM_SET_COMPARE(&htim1, TIM_CHANNEL_1,(uint32_t)pid_I.out);				// firts leg high switch

	}
}



void HAL_GPIO_EXTI_Callback(uint16_t GPIO_Pin)
{
  /* Prevent unused argument(s) compilation warning */
  UNUSED(GPIO_Pin);
  /* NOTE: This function Should not be modified, when the callback is needed,
           the HAL_GPIO_EXTI_Callback could be implemented in the user file
   */
		
if( (GPIO_Pin == HLL_1_Pin) |  (GPIO_Pin == HLL_2_Pin) | (GPIO_Pin == HLL_3_Pin) ){
	
	// disble the INT
	HAL_TIM_Base_Stop(&htim3);
	
	
	//__HAL_TIM_DISABLE_IT(&htim3);
	sensor[0]=HAL_GPIO_ReadPin(HLL_1_GPIO_Port,HLL_1_Pin);
	sensor[1]=HAL_GPIO_ReadPin(HLL_2_GPIO_Port,HLL_2_Pin);
	sensor[2]=HAL_GPIO_ReadPin(HLL_3_GPIO_Port,HLL_3_Pin);
	
	// time clcultion
	
	time_diff = (TIM3->CNT*1e-6);
	time_diff +=(time_tehif*1e-4);
	speed = (2.0*PI/3.0)/(time_diff*Pole_P);
	
	
	STEP=0;		
	FIND_MOTOR_STEP();
	APPLY_THE_PWMs(STEP);


	//HAL_UART_Transmit(&huart1,"HII",3,10);
	time_tehif = 0;
	TIM3->CNT = 0;
	HAL_TIM_Base_Start(&htim3);

	}else{

	}	
}





// Steps function --> this functions Takes no rguments and returns no arguments, just declare
// a GLOBAL variable called STEP
void FIND_MOTOR_STEP(void){
	
		// Cheack for the step
		if( sensor[0] == 1 && sensor[1] == 0 && sensor[2] == 0 ){         // step 6  //100
			STEP = 6;
			
    }    
    else if( sensor[0] == 0 && sensor[1] == 1 && sensor[2] == 0 ){  // step 4  //010  
			STEP = 4;
			
    }
    else if( sensor[0] == 1 && sensor[1] == 1 && sensor[2] == 0){  // step 5  //110
			STEP = 5;
			
    }
    else if( sensor[0] == 0 && sensor[1] == 0 && sensor[2] ==1 ){   // step 2  //001
			STEP = 2;
			
    }
    else if( sensor[0] == 1 && sensor[1] ==0 && sensor[2] ==1 ){    // step 1  //101
			STEP = 1;
			
    }
    else if( sensor[0] == 0 && sensor[1] == 1 && sensor[2] == 1 ){  // step 3  //011
			STEP = 3;
			
    }
		else{
			STEP = 0;
			
    }	
		
}






void APPLY_THE_PWMs(uint8_t step){
	
    switch (step) {
			
      case 1:
				__HAL_TIM_SET_COMPARE(&htim1, TIM_CHANNEL_1,(uint32_t)pid_I.out);				// firts leg high switch
				__HAL_TIM_SET_COMPARE(&htim1, TIM_CHANNEL_2,(uint32_t)0);														// first leg low switch
				
				__HAL_TIM_SET_COMPARE(&htim1, TIM_CHANNEL_3,(uint32_t)0);														// second leg high switch
				__HAL_TIM_SET_COMPARE(&htim2, TIM_CHANNEL_1,(uint32_t)pid_I.out);				// second leg low switch
				
				__HAL_TIM_SET_COMPARE(&htim2, TIM_CHANNEL_3,(uint32_t)0);														// third leg high switch
				__HAL_TIM_SET_COMPARE(&htim2, TIM_CHANNEL_4,(uint32_t)0);														// third leg low switch
        break;
        
      case 2:
				__HAL_TIM_SET_COMPARE(&htim1, TIM_CHANNEL_1,(uint32_t)0);
				__HAL_TIM_SET_COMPARE(&htim1, TIM_CHANNEL_2,(uint32_t)0);
			
				__HAL_TIM_SET_COMPARE(&htim1, TIM_CHANNEL_3,(uint32_t)pid_I.out);
				__HAL_TIM_SET_COMPARE(&htim2, TIM_CHANNEL_1,(uint32_t)0);
			
				__HAL_TIM_SET_COMPARE(&htim2, TIM_CHANNEL_3,(uint32_t)0);
				__HAL_TIM_SET_COMPARE(&htim2, TIM_CHANNEL_4,(uint32_t)pid_I.out);
        break;

      case 3:
				__HAL_TIM_SET_COMPARE(&htim1, TIM_CHANNEL_1,(uint32_t)pid_I.out);
				__HAL_TIM_SET_COMPARE(&htim1, TIM_CHANNEL_2,(uint32_t)0);
			
				__HAL_TIM_SET_COMPARE(&htim1, TIM_CHANNEL_3,(uint32_t)0);
				__HAL_TIM_SET_COMPARE(&htim2, TIM_CHANNEL_1,(uint32_t)0);
			
				__HAL_TIM_SET_COMPARE(&htim2, TIM_CHANNEL_3,(uint32_t)0);
				__HAL_TIM_SET_COMPARE(&htim2, TIM_CHANNEL_4,(uint32_t)pid_I.out);
        break;
        
      case 4:
				__HAL_TIM_SET_COMPARE(&htim1, TIM_CHANNEL_1,(uint32_t)pid_I.out);
				__HAL_TIM_SET_COMPARE(&htim1, TIM_CHANNEL_2,(uint32_t)0);
			
				__HAL_TIM_SET_COMPARE(&htim1, TIM_CHANNEL_3,(uint32_t)0);
				__HAL_TIM_SET_COMPARE(&htim2, TIM_CHANNEL_1,(uint32_t)pid_I.out);
			
				__HAL_TIM_SET_COMPARE(&htim2, TIM_CHANNEL_3,(uint32_t)0);
				__HAL_TIM_SET_COMPARE(&htim2, TIM_CHANNEL_4,(uint32_t)0);
        break;
        
      case 5:
				__HAL_TIM_SET_COMPARE(&htim1, TIM_CHANNEL_1,(uint32_t)0);
				__HAL_TIM_SET_COMPARE(&htim1, TIM_CHANNEL_2,(uint32_t)0);
			
				__HAL_TIM_SET_COMPARE(&htim1, TIM_CHANNEL_3,(uint32_t)0);
				__HAL_TIM_SET_COMPARE(&htim2, TIM_CHANNEL_1,(uint32_t)pid_I.out);
			
				__HAL_TIM_SET_COMPARE(&htim2, TIM_CHANNEL_3,(uint32_t)pid_I.out);
				__HAL_TIM_SET_COMPARE(&htim2, TIM_CHANNEL_4,(uint32_t)0);
        break;
        
      case 6:
				__HAL_TIM_SET_COMPARE(&htim1, TIM_CHANNEL_1,(uint32_t)0);
				__HAL_TIM_SET_COMPARE(&htim1, TIM_CHANNEL_2,(uint32_t)pid_I.out);
			
				__HAL_TIM_SET_COMPARE(&htim1, TIM_CHANNEL_3,(uint32_t)0);
				__HAL_TIM_SET_COMPARE(&htim2, TIM_CHANNEL_1,(uint32_t)0);
	
				__HAL_TIM_SET_COMPARE(&htim2, TIM_CHANNEL_3,(uint32_t)pid_I.out);
				__HAL_TIM_SET_COMPARE(&htim2, TIM_CHANNEL_4,(uint32_t)0);
        break;
			case 0:
				__HAL_TIM_SET_COMPARE(&htim1, TIM_CHANNEL_1,(uint32_t)0);				// firts leg high switch
				__HAL_TIM_SET_COMPARE(&htim1, TIM_CHANNEL_2,(uint32_t)0);				// first leg low switch

				__HAL_TIM_SET_COMPARE(&htim1, TIM_CHANNEL_3,(uint32_t)0);				// second leg high switch
				__HAL_TIM_SET_COMPARE(&htim2, TIM_CHANNEL_1,(uint32_t)0);				// second leg low switch

				__HAL_TIM_SET_COMPARE(&htim2, TIM_CHANNEL_3,(uint32_t)0);				// third leg high switch
				__HAL_TIM_SET_COMPARE(&htim2, TIM_CHANNEL_4,(uint32_t)0);				// third leg low switch				
							
      default:
				__HAL_TIM_SET_COMPARE(&htim1, TIM_CHANNEL_1,(uint32_t)0);
				__HAL_TIM_SET_COMPARE(&htim1, TIM_CHANNEL_2,(uint32_t)0);
				__HAL_TIM_SET_COMPARE(&htim1, TIM_CHANNEL_3,(uint32_t)0);

				__HAL_TIM_SET_COMPARE(&htim2, TIM_CHANNEL_1,(uint32_t)0);
				__HAL_TIM_SET_COMPARE(&htim2, TIM_CHANNEL_3,(uint32_t)0);
				__HAL_TIM_SET_COMPARE(&htim2, TIM_CHANNEL_4,(uint32_t)0);
        break;
			
  }  
}






/* USER CODE END 4 */
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


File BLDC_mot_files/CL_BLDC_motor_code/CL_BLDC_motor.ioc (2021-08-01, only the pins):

Mcu.UserName=STM32F103C8Tx
PA6.GPIO_Label=HLL_2
PD1-OSC_OUT.Signal=RCC_OSC_OUT
PB6.Signal=USART1_TX
PB7.Signal=USART1_RX
PA8.Signal=S_TIM1_CH1
PA6.Signal=GPXTI6
PA10.Signal=S_TIM1_CH3
PA15.Signal=S_TIM2_CH1_ETR
PA3.Signal=ADCx_IN3
PC13-TAMPER-RTC.Signal=GPIO_Output
PD0-OSC_IN.Signal=RCC_OSC_IN
PA0-WKUP.Signal=ADCx_IN0
PA13.Signal=SYS_JTMS-SWDIO
PA9.Signal=S_TIM1_CH2
PA1.Signal=ADCx_IN1
PB10.Signal=S_TIM2_CH3
PA5.Signal=GPXTI5
PA2.Signal=ADCx_IN2
PB3.Signal=S_TIM2_CH2
PA7.GPIO_Label=HLL_3
PA5.GPIO_Label=HLL_1
PA14.Signal=SYS_JTCK-SWCLK
PA7.Signal=GPXTI7

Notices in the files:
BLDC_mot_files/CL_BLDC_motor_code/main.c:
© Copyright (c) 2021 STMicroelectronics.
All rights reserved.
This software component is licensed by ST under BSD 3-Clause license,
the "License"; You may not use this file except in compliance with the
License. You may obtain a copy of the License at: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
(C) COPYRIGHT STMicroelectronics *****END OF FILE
